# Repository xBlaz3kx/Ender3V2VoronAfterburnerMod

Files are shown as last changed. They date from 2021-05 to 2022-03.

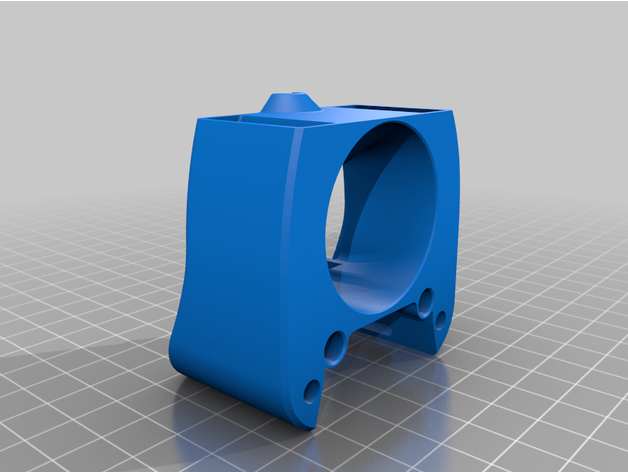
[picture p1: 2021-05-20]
STLs/MicroswissToolheadForAfterburner/images/printhead_front_microswiss.png

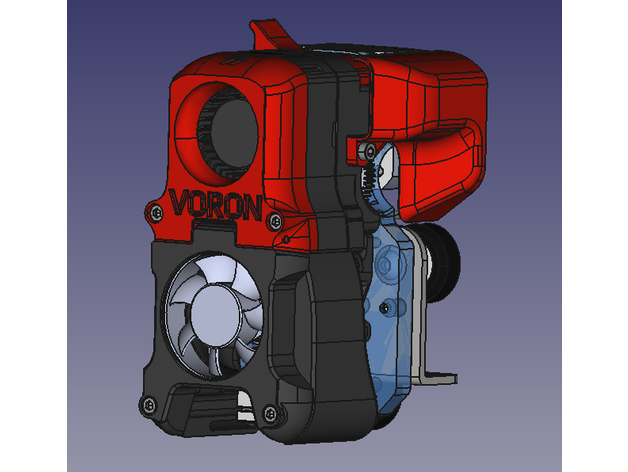
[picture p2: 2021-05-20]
STLs/Ender3BackplateAdapter/images/screenshot-20201004084634.png

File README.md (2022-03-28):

# Ender 3 V2 Voron Afterburner Mod

## About

This project is a modification of the Ender 3 V2, replacing the original print head with
a [Voron Afterburner](https://github.com/VoronDesign/Voron-Afterburner). All the parts needed for this modification are
listed in [BOM](#bill-of-materials). The part of the mod is changing the firmware
to [Klipper](https://www.klipper3d.org/) instead of Marlin, which is optional and can be done separately.

**_Disclaimer: Follow these instructions at your own risk._**

## Bill of materials

| Item | # |
| :---: | :---: |
| Genuine or clone Micro Swiss hotend | 1 |
| Genuine or clone BMG extruder or it's parts | 1 |
| Filament (PETG or ABS)| around 150g |
| Raspberry Pi 3 or 4 | 1 |
| Power supply for RPi 3/4 | 1 |
| 4020 blower/radial fan | 1 |
| 4010 axial fan | 1 |
| Heat inserts M3 | 11 |
| M3x40 screws | 4 |
| M3x30 screws | 5 |
| M3x20 screws | 2 |
| M3x16 screws | 2 |
| M3x12 screws | 2|
| M3x8 screws | 4 |
| M3 spacers |*4|
| M4 spacers | *1 |
| 24 AWG wire | around 2m  |
| *Optional: BTT SKR Mini E3 V2 | 1 |

## Printing and assembly

### Tools required

1. Soldering Iron
2. Cutters
3. Allen keys
4. Crimpers
5. 3D printer

### Printing the parts

It is recommended to print the hotend assembly parts with temperature-resistant materials such as PETG or ABS. Voron
design team recommends using primary and accent color (for more information, check out
their [docs](https://docs.vorondesign.com/)). They recommend printing the parts with 40% infill and 4 outer walls.

### Assembly

_Detailed assembly instructions coming soon.._

## Klipper installation and configuration

### Installing Fluidd

Installing [Fluidd](https://github.com/cadriel/fluidd), the Klipper WebUI, is fairly straightforward:

Download the Raspberry Pi image [here](https://github.com/cadriel/FluiddPI/releases/latest)
or clone the [repository](https://github.com/cadriel/fluidd) onto an existing OS. After downloading, flash the image to
a SD card. Insert the card into the Raspberry Pi, and you're set to go.

There are instances of running Fluidd and Klipper in Docker, so you could also try that.

### Klipper

#### Installation

To install Klipper:

    ```
    cd klipper/
    make menuconfig
    ```

*This step is for SKR Mini E3 V2*

1. Select "_Enable extra-low level configuration_"
    - STM32F1
    - STM32F103
2. Bootloader Offset: 28KiB bootloader
3. USB for communication
4. Enter the USB ID. You can find them by `lsusb -v`. Vendor ID should be `0x1eaf`, USB Device ID should be `0x0004` and USB
   Serial Number is the "iSerial" from lsusb -v, so 0.
5. Put !PA14 into the GPIO Pins
6. Save the config

Then compile the firmware:

```
make clean #use when updating firmware!
make
```

When compiled, copy and rename the **klipper.bin** file in _/klipper/out/_ folder to **firmware.bin** (check your board
for naming convention) and copy it to an SD card. Turn off the printer and insert the card. Turn on the printer. The
firmware should be flashed.

Then find the USB ID:

``` 
 ls /dev/serial/by-id/*
```
Change the serial in **printer.cfg**:

```
   [mcu]
   serial: /dev/serial/by-id/usb-1a86_USB2.0-Serial-if00-port0
```

#### Configuring Klipper

Since I've got a BTT SKR Mini E3 V2 board, I copied the configuration I found for this board and modified it to suit my
printer. The configuration file is attached and there are marks where any additional changes are required.

Copy the printer.cfg to _klipper_config/_.

## Helpful docs:

- [Calibration guide](https://teachingtechyt.github.io/calibration.html)
- [Voron docs](https://docs.vorondesign.com/)
- [Klipper installation from Reddit](https://www.reddit.com/r/BIGTREETECH/comments/cxjiwx/skr_mini_e3_any_help_with_klipper/ezp5oiw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)

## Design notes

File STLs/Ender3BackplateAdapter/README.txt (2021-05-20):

Voron afterburner mount for Ender 3 (bmg direct drive) by igalopaka on Thingiverse: https://www.thingiverse.com/thing:4614384

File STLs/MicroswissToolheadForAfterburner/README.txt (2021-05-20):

VORON printhead for MicroSwiss hotend by phil245 on Thingiverse: https://www.thingiverse.com/thing:4705446

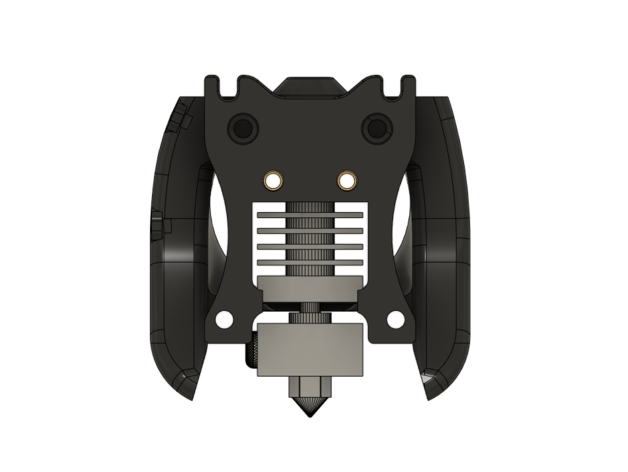
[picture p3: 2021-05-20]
STLs/MicroswissToolheadForAfterburner/images/Back.PNG

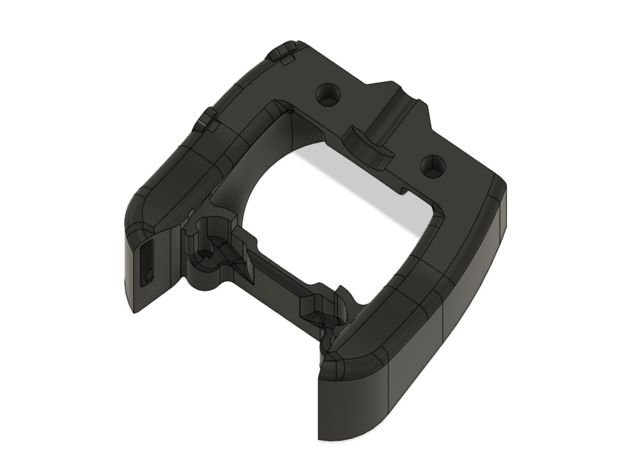
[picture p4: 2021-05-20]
STLs/MicroswissToolheadForAfterburner/images/Front_Mount.PNG

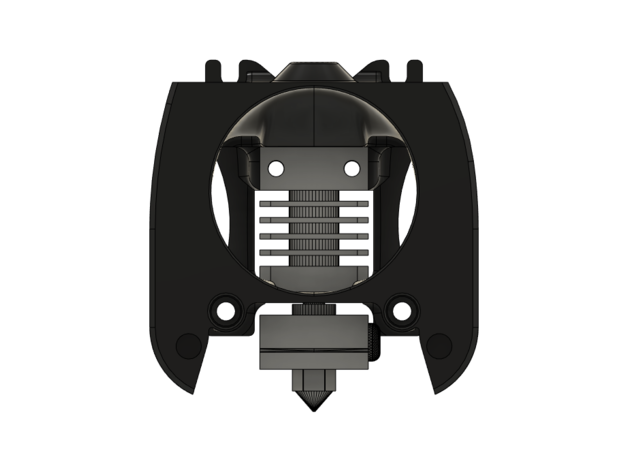
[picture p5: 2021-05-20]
STLs/MicroswissToolheadForAfterburner/images/Front.PNG

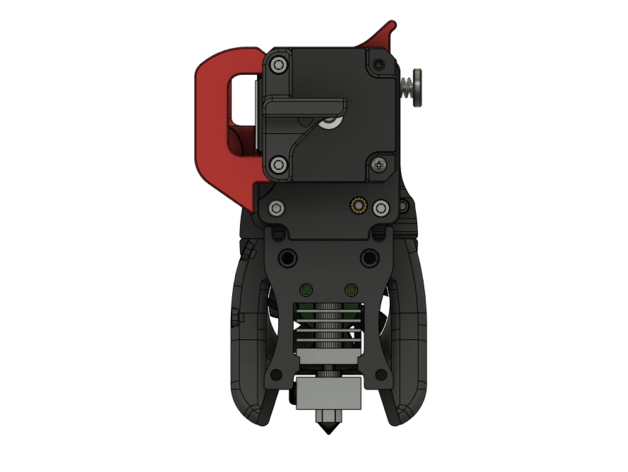
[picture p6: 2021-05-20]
STLs/MicroswissToolheadForAfterburner/images/Back_Complete.PNG

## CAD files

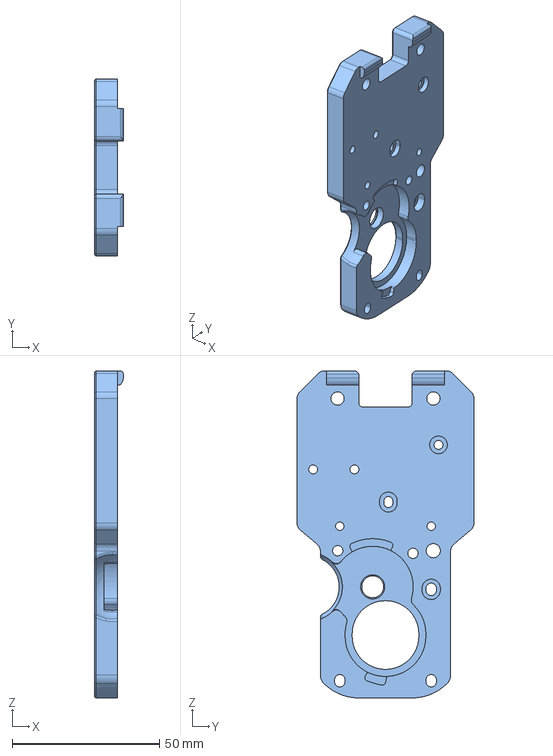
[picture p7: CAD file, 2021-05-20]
STLs/Ender3BackplateAdapter/files/afterburner-motor-plate-ender3pro.step
9.70 x 60.0 x 110.9 mm

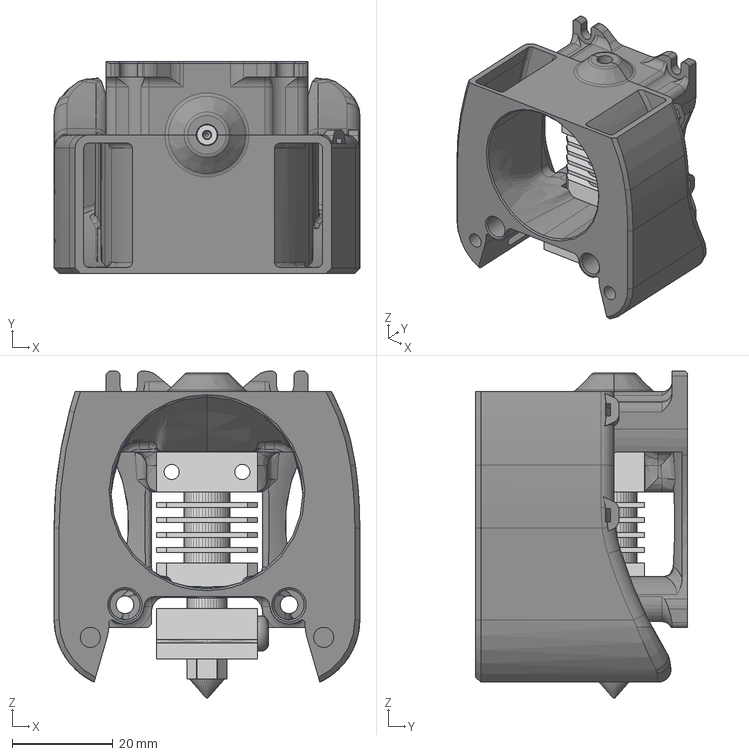
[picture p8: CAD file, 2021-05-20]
STLs/MicroswissToolheadForAfterburner/files/printhead_mount_microswiss_v2.step
60.6 x 41.9 x 64.8 mm

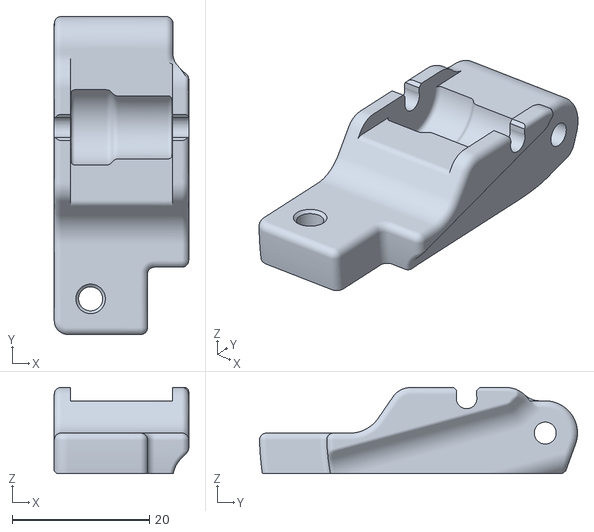
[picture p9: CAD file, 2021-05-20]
STLs/VoronAfterburner/DirectFeed/[a]_guidler.stl
19.6 x 46.3 x 12.5

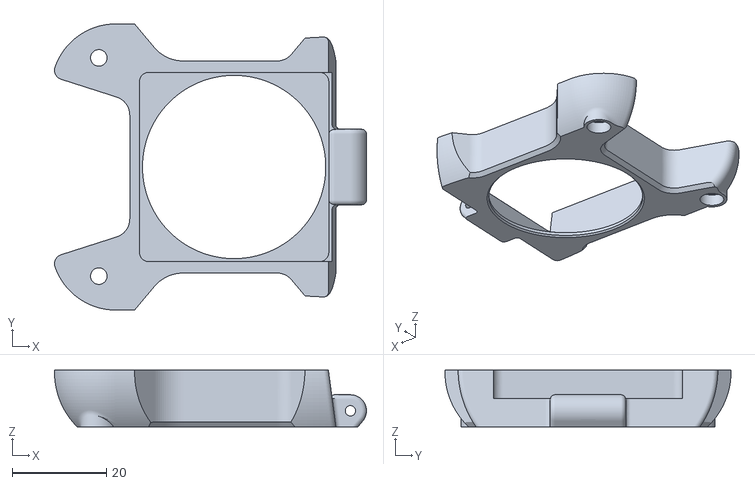
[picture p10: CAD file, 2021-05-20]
STLs/VoronAfterburner/hotend_fan_mount.stl
66.1 x 60.6 x 12.0

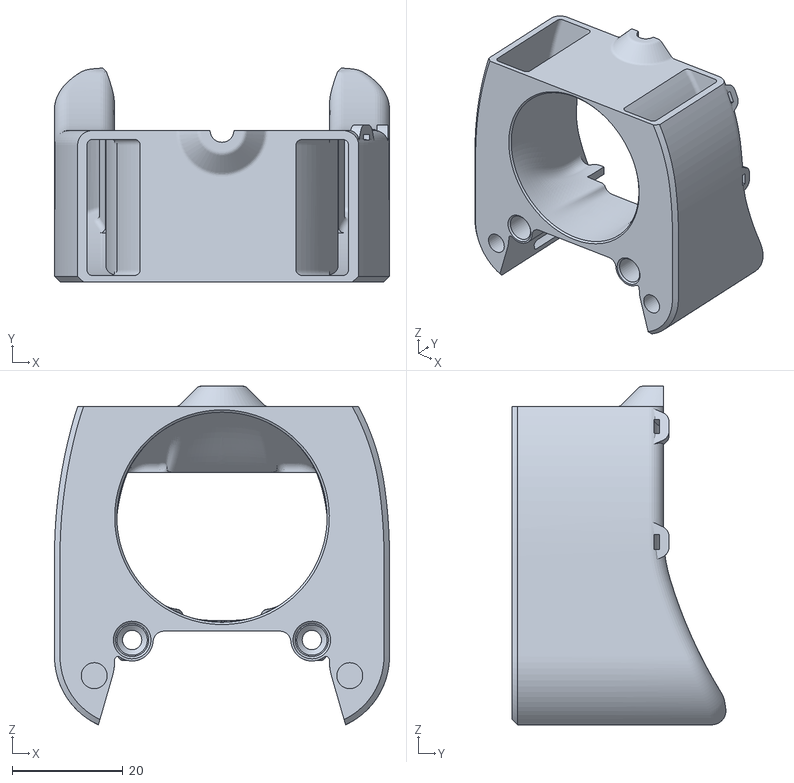
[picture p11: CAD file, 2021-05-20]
STLs/MicroswissToolheadForAfterburner/files/printhead_front_microswiss.stl
60.6 x 38.7 x 61.2

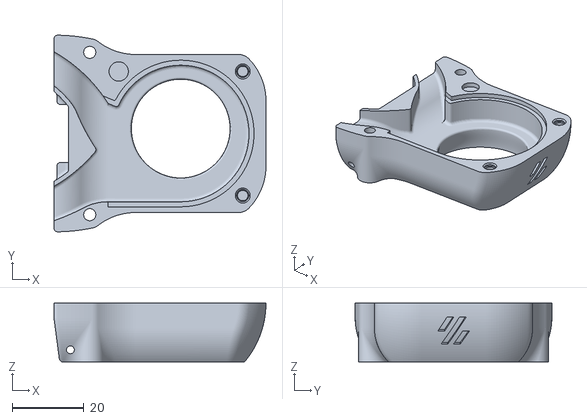
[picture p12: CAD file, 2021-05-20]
STLs/VoronAfterburner/[a]_blower_housing_front.stl
59.3 x 55.0 x 16.5

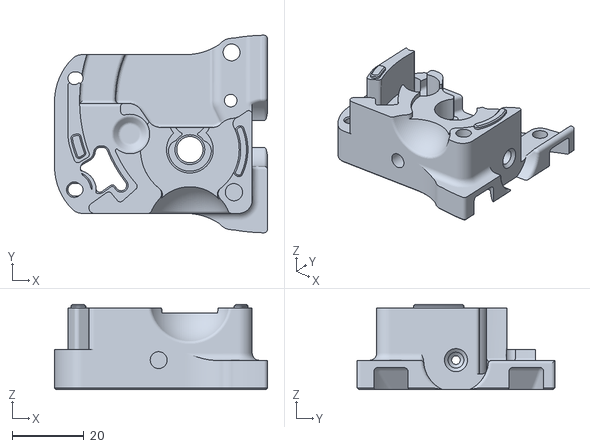
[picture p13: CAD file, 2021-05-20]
STLs/VoronAfterburner/DirectFeed/extruder_body.stl
59.3 x 55.0 x 23.7

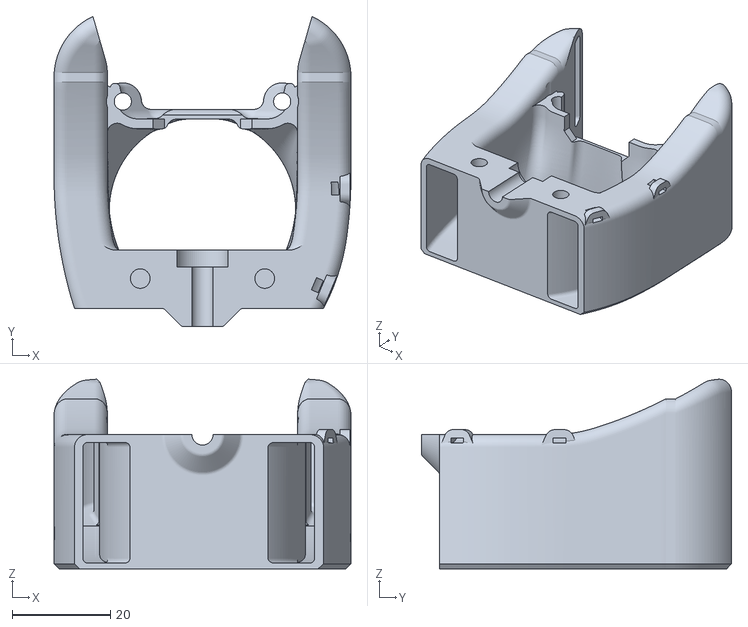
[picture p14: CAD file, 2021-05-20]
STLs/MicroswissToolheadForAfterburner/files/printhead_front_microswiss_v2.stl
60.6 x 63.2 x 38.7

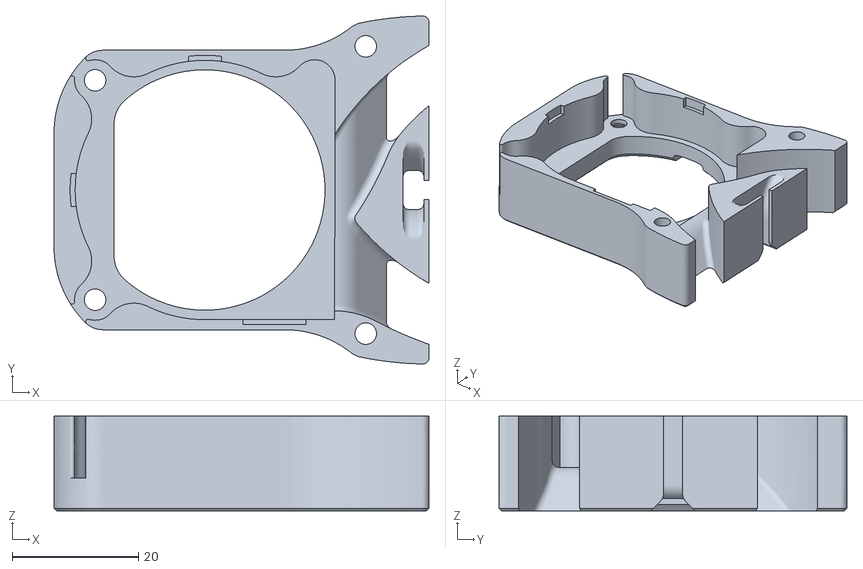
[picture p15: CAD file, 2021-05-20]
STLs/VoronAfterburner/blower_housing_rear.stl
59.3 x 55.0 x 15.0

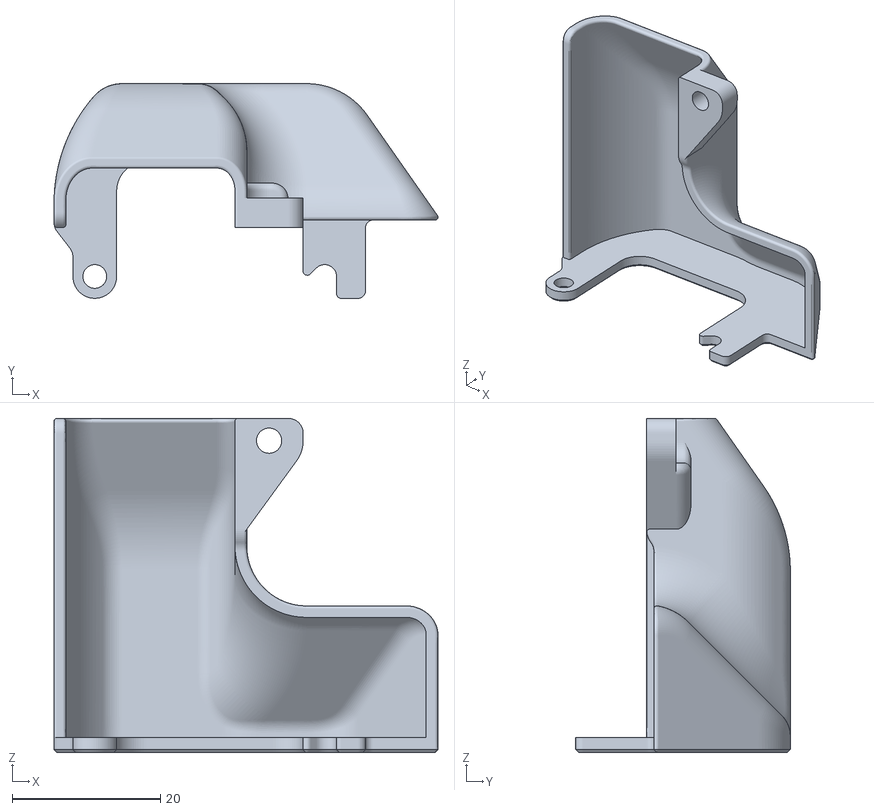
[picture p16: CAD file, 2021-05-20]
STLs/VoronAfterburner/DirectFeed/[a]_connector_cover_V2.4.stl
51.8 x 29.0 x 45.1

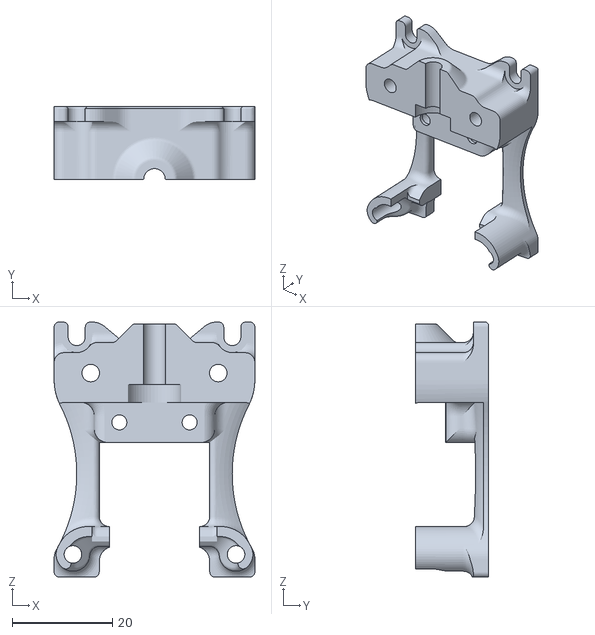
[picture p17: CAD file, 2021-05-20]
STLs/MicroswissToolheadForAfterburner/files/printhead_rear_microswiss.stl
40.0 x 14.5 x 50.8

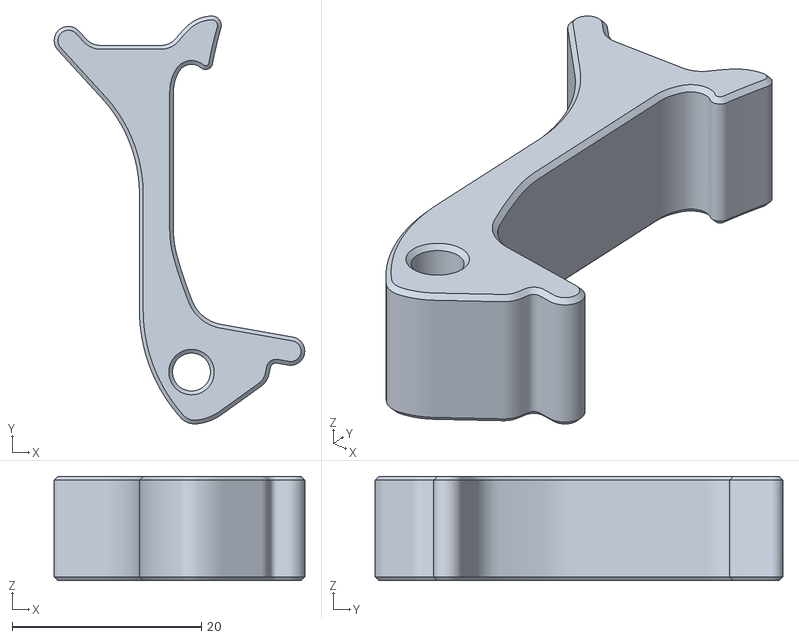
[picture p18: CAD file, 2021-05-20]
STLs/VoronAfterburner/DirectFeed/[a]_latch.stl
26.5 x 43.1 x 11.0

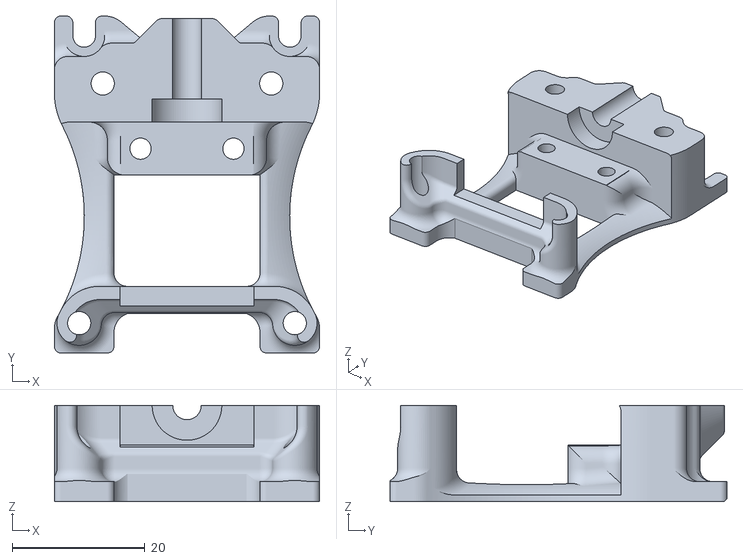
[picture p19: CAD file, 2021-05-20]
STLs/MicroswissToolheadForAfterburner/files/printhead_rear_microswiss_v2.stl
40.0 x 50.8 x 14.5

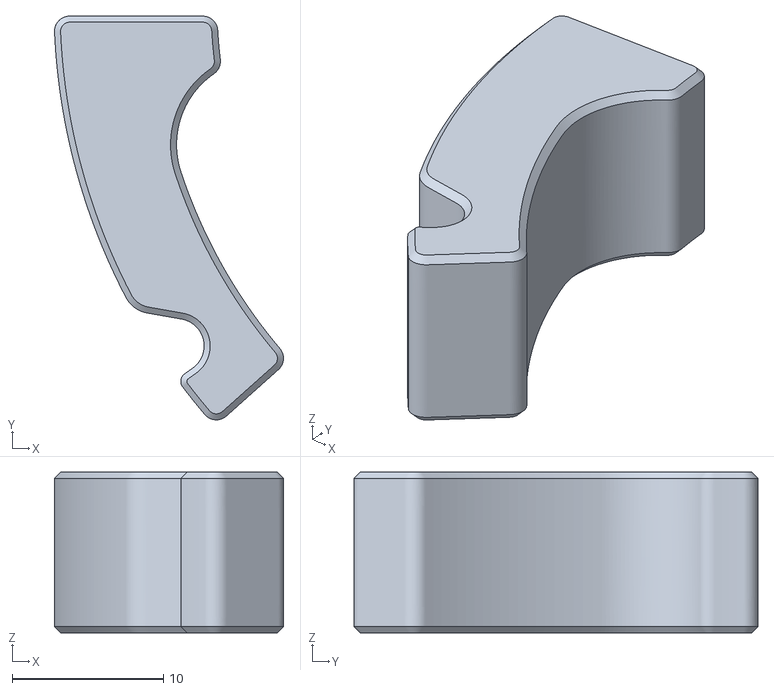
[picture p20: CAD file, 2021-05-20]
STLs/VoronAfterburner/DirectFeed/latch_shuttle.stl
15.1 x 26.7 x 10.6

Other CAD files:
STLs/Ender3BackplateAdapter/files/afterburner-motor-plate-ender3-UNTESTED.step
STLs/Ender3BackplateAdapter/files/afterburner-motor-plate-ender3v2-UNTESTED.step
STLs/Ender3BackplateAdapter/files/afterburner-motor-plate-ender3-UNTESTED.stl
STLs/Ender3BackplateAdapter/files/afterburner-motor-plate-ender3pro.stl
STLs/Ender3BackplateAdapter/files/afterburner-motor-plate-ender3v2-UNTESTED.stl

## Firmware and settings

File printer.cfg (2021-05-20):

# This file contains common pin mappings for the BIGTREETECH SKR mini
# E3 v2.0. To use this config, the firmware should be compiled for the
# STM32F103 with a "28KiB bootloader" and USB communication. Also,
# select "Enable extra low-level configuration options" and configure
# "GPIO pins to set at micro-controller startup" to "!PA14".

# The "make flash" command does not work on the SKR mini E3. Instead,
# after running "make", copy the generated "out/klipper.bin" file to a
# file named "firmware.bin" on an SD card and then restart the SKR
# mini E3 with that SD card.

# See docs/Config_Reference.md for a description of parameters.

# Do not delete those, otherwise you will get an error in Fluidd
[include client.cfg]
[include client_macros.cfg]

[stepper_x]
step_pin: PB13
dir_pin: !PB12
enable_pin: !PB14
microsteps: 16
rotation_distance: 40
endstop_pin: ^PC0
# This section was modified to get semi-accurate zero position of the X axis.
position_endstop = -18
position_min = -18
#
position_max: 235
homing_speed: 50

[tmc2209 stepper_x]
uart_pin: PC11
tx_pin: PC10
uart_address: 0
run_current: 0.580
hold_current: 0.500
stealthchop_threshold: 999999

[stepper_y]
step_pin: PB10
dir_pin: !PB2
enable_pin: !PB11
microsteps: 16
rotation_distance: 40
endstop_pin: ^PC1
# This section was modified to get semi-accurate zero position of the Y axis.
position_endstop = -8
position_min = -8
#
position_max: 235
homing_speed: 50

[tmc2209 stepper_y]
uart_pin: PC11
tx_pin: PC10
uart_address: 2
run_current: 0.580
hold_current: 0.500
stealthchop_threshold: 999999

[stepper_z]
step_pin: PB0
dir_pin: PC5
enable_pin: !PB1
microsteps: 16
rotation_distance: 8
endstop_pin: ^PC2
position_endstop: 0.0
position_max: 250

[tmc2209 stepper_z]
uart_pin: PC11
tx_pin: PC10
uart_address: 1
run_current: 0.580
hold_current: 0.500
stealthchop_threshold: 999999

[extruder]
max_extrude_only_distance: 100.0
step_pin: PB3
# I had to switch the direction pin to negative logic.
dir_pin: PB4
enable_pin: !PD2
microsteps: 16
# This is the value I got. Voron documentation suggest it should be 22.67, but this is what I calculated from their guide.
rotation_distance: 7
nozzle_diameter: 0.400
filament_diameter: 1.750
heater_pin: PC8
sensor_type: EPCOS 100K B57560G104F
sensor_pin: PA0
#control: pid
#pid_Kp: 21.527
#pid_Ki: 1.063
#pid_Kd: 108.982
min_temp: 0
max_temp: 270

[tmc2209 extruder]
uart_pin: PC11
tx_pin: PC10
uart_address: 3
run_current: 0.650
hold_current: 0.500
stealthchop_threshold: 999999

[heater_bed]
heater_pin: PC9
sensor_type: ATC Semitec 104GT-2
sensor_pin: PC3
#control: pid
#pid_Kp: 54.027
#pid_Ki: 0.770
#pid_Kd: 948.182
min_temp: 0
max_temp: 100

[heater_fan nozzle_cooling_fan]
pin: PC7

[fan]
pin: PC6

[mcu]
# You should change this section, since every board will have an unique serial ID.
serial: /dev/serial/by-id/usb-Klipper_stm32f103xe_<id>-if00

[printer]
kinematics: cartesian
max_velocity: 300
max_accel: 3000
max_z_velocity: 5
max_z_accel: 100

[static_digital_output usb_pullup_enable]
pins: !PA14

[board_pins]
aliases:
    # EXP1 header
    EXP1_1=PB5, EXP1_3=PA9,   EXP1_5=PA10, EXP1_7=PB8, EXP1_9=<GND>,
    EXP1_2=PA15, EXP1_4=<RST>, EXP1_6=PB9,  EXP1_8=PB15, EXP1_10=<5V>

# See the sample-lcd.cfg file for definitions of common LCD displays.

#*# <---------------------- SAVE_CONFIG ---------------------->
#*# DO NOT EDIT THIS BLOCK OR BELOW. The contents are auto-generated.
#*#
#*# [extruder]
#*# control = pid
#*# pid_kp = 23.941
#*# pid_ki = 1.108
#*# pid_kd = 129.281
#*#
#*# [heater_bed]
#*# control = pid
#*# pid_kp = 71.794
#*# pid_ki = 1.679
#*# pid_kd = 767.297
